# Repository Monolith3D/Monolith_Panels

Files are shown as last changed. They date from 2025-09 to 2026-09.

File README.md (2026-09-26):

# Monolith Panels for Voron 2.4 and Trident

### The 1515 extrusion version by CabbageCorp can be found [here](https://github.com/Monolith3D/Monolith_Panels/tree/main/Usermods/CabbageCorp/Mini_Monolith).

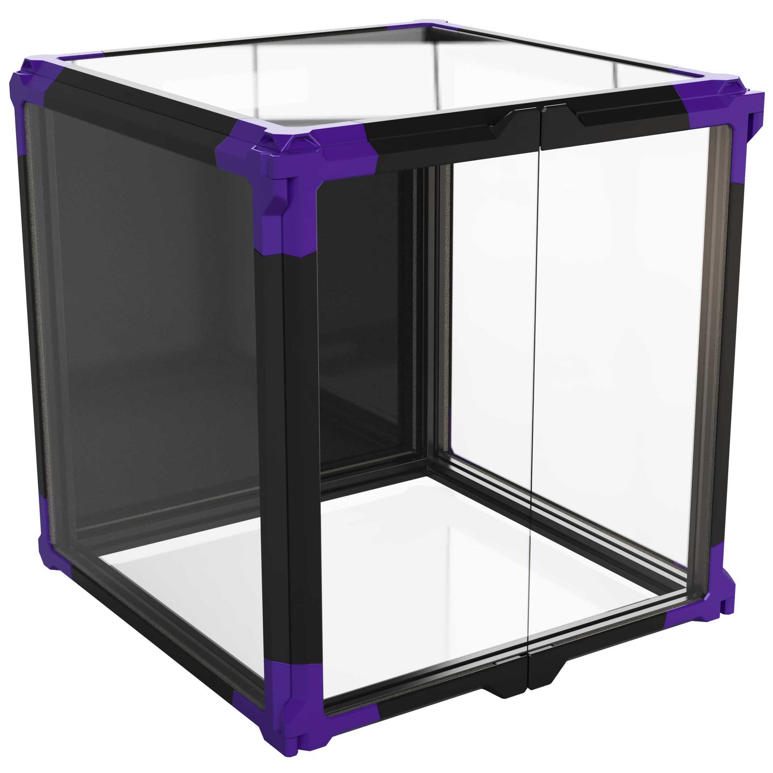
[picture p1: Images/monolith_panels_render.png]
Monolith Panels render


## What's this?

Overcomplicated panels.

## Repository contents

- [CAD](CAD/) - CAD files and assembly reference.
- [STLs](STLs/) - Printable STL files.
- [BOM](BOM/) - Variant BOM CSVs.
- [Images](Images/README.md) - Render gallery.
- [UserMods](Usermods/) - User mods and community additions.

## Use

- The CAD contains everything needed for V2/VT 250/300/350mm with BOM-thickness panels (3mm), and is also a good assembly guide.
- Parts will load in the correct orientation when exported.
- The vertical printed part length is based on theoretical Z travel, not bed size. Pick the vertical part length based on your machine's Z travel. Tridents usually have 250mm Z regardless of bed size, except the cubed kits.
- The panel system is intended to be used with another layer of 3mm foam tape, or with 5mm foam tape paired with 4mm panels. Monolith Gantry stepper protrusion is 4mm.
- The corners can be used without the straights, but your mileage may vary if you do not put VHB on them.
- When used as a panel frame, you can get away with putting VHB only in the middle.
- Clips are fairly sensitive to EM/PA, but can be scaled to fit the other plastic parts. They are not sensitive to aluminum extrusion tolerances.
- Recommended shrinkage compensation for ABS parts is 99.3-99.5%. Test this before committing to large prints, because shrinkage can add up to 3-4mm in total.
- Feel free to remix the parts for different setups.

## Community and support

> [!NOTE]
> **If you have questions or want to stay more up-to-date with Monolith, consider joining the dedicated Discord server.**
>
> Join the Discord (https://discord.gg/monolith3d)
>
> **If you would like to see more of this and other projects in the future, consider supporting Monolith on Patreon.**
>
> Support Monolith on Patreon (https://www.patreon.com/monolith3d)

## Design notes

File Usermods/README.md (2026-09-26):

# User Mods

This folder is for community-made additions, adaptations, and compatibility parts for Monolith Panels.

User mods are not official Monolith Panels files unless stated otherwise. Check the mod author, target printer, panel thickness, door or hinge assumptions, clip style, and clearance assumptions before printing or ordering parts.

Use the folder structure `username/usermod_name` for new user mods.

Good user mod folders should include:

- A short `README.md` explaining what the mod does
- Clear compatibility notes for the target printer, panel dimensions, panel thickness, clip style, and door or hinge setup where relevant
- STL, CAD, image, and BOM files needed to understand the mod
- Assembly notes or warnings if the mod changes panel fit, clips, hinges, handles, door closure, foam stack, or clearance
- Credit and license notes when the mod reuses work from another project

Use user mods at your own risk. They may not receive updates when the main Monolith Panels files change.

## Existing User Mods

| Mod | Author | What it does |
| --- | --- | --- |
| usermod_name | username | Briefly describe what the mod adds, adapts, or changes. |
| [Micronolith Panels](burkfers/Micronolith/) | burkfers | Adapts Mini Monolith panels for a Micron 180, including regular and Formbot vertical variants and Micron R1 handle-compatible horizontals. |
| [Mini Monolith](CabbageCorp/Mini_Monolith/) | CabbageCorp | Adapts Monolith Panels for 1515-extrusion PFA/V0-style printers with ZeroPanels-style clips, panel frames, corners, hinges, and related print files. |
| [Monolith Panels Parametric](mjlo/Monolith%20Panels%20Parametric/) | mjlo | Provides parametric Fusion CAD for Monolith-inspired panels, mainly to support thicker panel material. |
| [Parametric with Annex clips](nvrprfct/parametric_with_annex_clips/) | nvrprfct | Adds Annex-style panel clips and corner/key files to Monolith Panels, with stock-size files and parametric CAD for custom panel stacks. |
| [Middle hinge](SaLei/Middle_hinge/) | SaLei | Provides a middle hinge file and reference image for Monolith Panels. |
| [ClickyClakyMod](TessaKavanagh/ClickyClakyMod/) | TessaKavanagh | Adds spacers and optional replacement ClickyClacky-style parts for adapting the door hinge/latch setup to Monolith Panels. |
|  | your name here :) |  |

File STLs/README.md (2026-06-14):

# STLs

Size-specific horizontal and vertical parts are grouped into subfolders, while shared clips, corners, clamps, and handle parts are kept here at the root.

Use the matching [BOM](../BOM/) to check which files and quantities are needed for a specific panel set.

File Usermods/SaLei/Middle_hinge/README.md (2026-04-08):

# Middle hinges

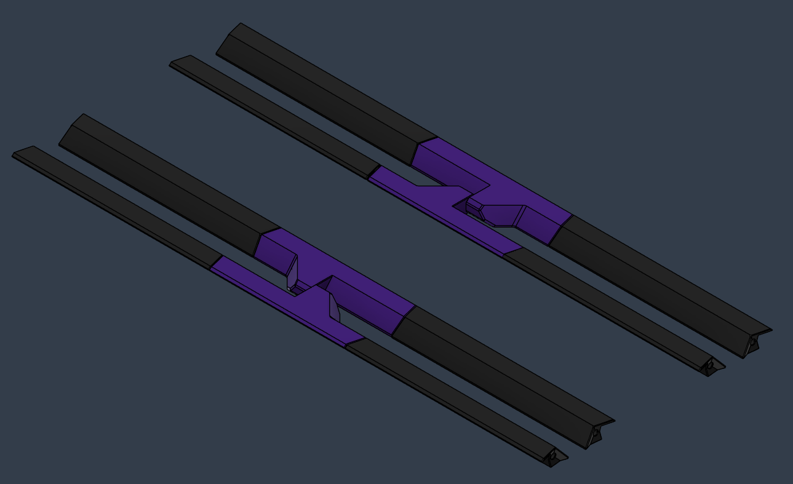
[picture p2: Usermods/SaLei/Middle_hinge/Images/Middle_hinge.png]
Middle_hinge


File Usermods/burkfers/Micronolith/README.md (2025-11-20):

# Micronolith Panels

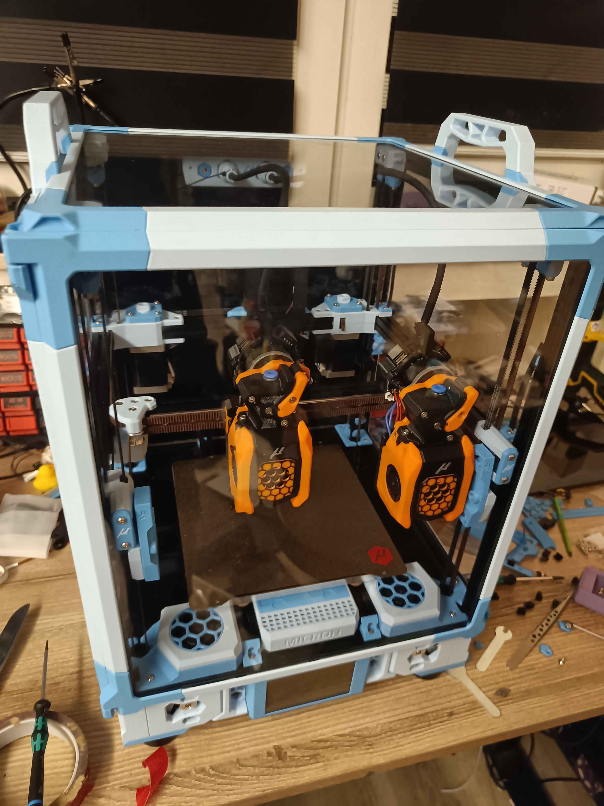
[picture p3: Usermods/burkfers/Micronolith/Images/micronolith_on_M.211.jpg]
Micronolith pannels displayed on M.211


This is an adaptation of CabbageCorp's [Mini Monolith](../../CabbageCorp/Mini_Monolith/) for a Micron 180.

The vertical exists in two variants: Regular, for to-spec panels, and Formbot, whose panels are approximately 2mm taller than the cad vertically.

Side and top horizontals are provided to fit the Micron R1 handles. If you do not wish to use handles, print 4 more horizontals instead.

Please see Mini Monolith for the corner pieces, clips, and more detailed instructions.

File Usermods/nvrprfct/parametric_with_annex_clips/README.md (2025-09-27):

# parametric monolith panels with annex clips
a few files for adding annex clips to the monolith panels. 

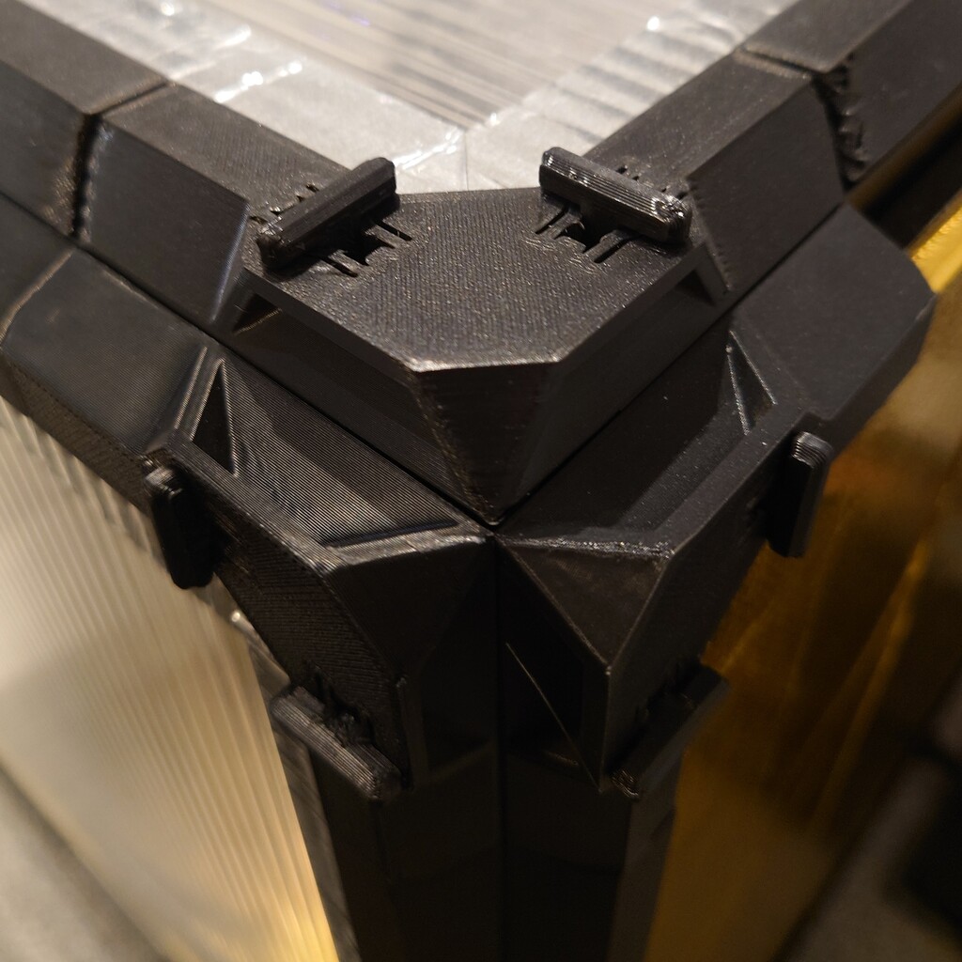
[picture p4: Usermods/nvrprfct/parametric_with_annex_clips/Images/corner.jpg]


## files:
### STLs/monolithStock_annex
- **STLs/monolithStock_annexCorner.step**
- **STLs/monolithStock_annexKey.3mf**

premade files for the stock monolith panel dimensions. you'll still need everything from the original monolith panels, except the corner body. 

print 2x keys for each corner.

### CAD/monolith_annex_mashup_variable_height
- **CAD/monolith_annex_mashup_variable_height.f3d**
- **[key_asymmetric_10.STEP](https://github.com/Annex-Engineering/Annex-Engineering_User_Mods/tree/main/Printers/All_Printers/annex_dev-Panel_2020_Clips_and_Hinges/panel_clips_and_corners/key/CA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)** (or another size)

the full f3d file with parametric history, so that you can custom make your own panel thickness, foam thickness, etc. 
includes corner body, and edge body. does ***not*** include support for hinges, or doors. 
for the key to be the right size, you'll need to download the key from the annex panels repo, split the key in the middle, then lengthen the middle by (panel_height_total - panel_height_outside - key_height - 0.1). where key_height would be 10 for key_asymmetric_10.STEP. 

be warned, I haven't updated the file in a minute, and it might have funny behaviour on large or small heights. I've been meaning to get around to this mod and clean it up, but life happens. 

### credits
[monolith panels by cloakedwayne](https://github.com/Monolith3D/Monolith_Panels)

[annex clips by annex engineering](https://github.com/Annex-Engineering/Annex-Engineering_User_Mods/tree/main/Printers/All_Printers/annex_dev-Panel_2020_Clips_and_Hinges)

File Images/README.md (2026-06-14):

# Preview

| Image | Image |
| --- | --- |
| [<br>Monolith Panels render](monolith_panels_render.png) | [<br>Corner closeup](corner_closeup.png) |
| [<br>Distant view](distant_view.png) | [<br>Inside view](inside.png) |
| [<br>Printed parts spread out](spread_out.png) | [<br>Upside down view](upside_down.png) |

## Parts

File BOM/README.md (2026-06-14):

# Monolith Panels BOM

## V2 250mm

| Amount | Item | Description |
| --- | --- | --- |
| 32 pcs | M3 nut | M3 hex nut. |
| 32 pcs | M3X16 SHCS | Socket head cap screw. |
| 28 pcs | M3X6 BHCS | Button head cap screw. |
| 28 pcs | M3xD5x4 threaded insert | Heat-set threaded insert. |
| 8 m | Foam tape | An additional layer of the same foam 3mm thick tape from the Voron BOM. |
| 1.5 m | VHB tape | VHB tape for adhesive mounting. |
| 0.1 m | 4mm OD PTFE tube | PTFE tube for the hinges. |
| 8 pcs | [`250mm_horizontal_side_x8.stl`](../STLs/Horizontals/250mm_horizontal_side_x8.stl) | Horizontal side piece for the 250mm panel set. |
| 2 pcs | [`250mm_horizontal_door_a_x2.stl`](../STLs/Horizontals/250mm_horizontal_door_a_x2.stl) | Door horizontal printed piece, A. |
| 2 pcs | [`250mm_horizontal_door_b_x2.stl`](../STLs/Horizontals/250mm_horizontal_door_b_x2.stl) | Door horizontal printed piece, B. |
| 6 pcs | [`V2_250mm_vertical_side_x6.stl`](../STLs/Verticals/V2_250mm_vertical_side_x6.stl) | Vertical side piece for the V2 250mm panel set. |
| 12 pcs | [`[a]_corner_x12.stl`](../STLs/%5Ba%5D_corner_x12.stl) | Universal corner printed part. |
| 2 pcs | [`[a]_hinge_a_x2.stl`](../STLs/Hinges/%5Ba%5D_hinge_a_x2.stl) | Universal hinge printed part, A. |
| 2 pcs | [`[a]_hinge_b_x2.stl`](../STLs/Hinges/%5Ba%5D_hinge_b_x2.stl) | Universal hinge printed part, B. |
| 2 pcs | [`[a]_hinge_c_x2.stl`](../STLs/Hinges/%5Ba%5D_hinge_c_x2.stl) | Universal hinge printed part, C. |
| 2 pcs | [`[a]_hinge_d_x2.stl`](../STLs/Hinges/%5Ba%5D_hinge_d_x2.stl) | Universal hinge printed part, D. |
| 60 pcs | [`clip_x60.stl`](../STLs/clip_x60.stl) | Printed panel clip. |
| 20 pcs | [`corner_clamp_BHCS_x20.stl`](../STLs/corner_clamp_BHCS_x20.stl) | Corner clamp for BHCS fastener. |
| 4 pcs | [`door_handle_clamp_x4.stl`](../STLs/door_handle_clamp_x4.stl) | Printed clamp for the door handle. |
| 735.8 cm3 | Total printed part volume | Total printed plastic volume for the printed parts listed above. |
| 650-800 g | Estimated filament use (ABS, Voron settings) | Estimated filament weight for normal unfilled ABS. |
| 700-900 g | Estimated filament use (ABS CF/GF, Voron settings) | Estimated filament weight for filled ABS. |

## V2 300mm

| Amount | Item | Description |
| --- | --- | --- |
| 32 pcs | M3 nut | M3 hex nut. |
| 32 pcs | M3X16 SHCS | Socket head cap screw. |
| 28 pcs | M3X6 BHCS | Button head cap screw. |
| 28 pcs | M3xD5x4 threaded insert | Heat-set threaded insert. |
| 9 m | Foam tape | An additional layer of the same foam 3mm thick tape from the Voron BOM. |
| 1.5 m | VHB tape | VHB tape for adhesive mounting. |
| 0.1 m | 4mm OD PTFE tube | PTFE tube for the hinges. |
| 8 pcs | [`300mm_horizontal_side_x8.stl`](../STLs/Horizontals/300mm_horizontal_side_x8.stl) | Horizontal side piece for the 300mm panel set. |
| 2 pcs | [`300mm_horizontal_door_a_x2.stl`](../STLs/Horizontals/300mm_horizontal_door_a_x2.stl) | Door horizontal printed piece, A. |
| 2 pcs | [`300mm_horizontal_door_b_x2.stl`](../STLs/Horizontals/300mm_horizontal_door_b_x2.stl) | Door horizontal printed piece, B. |
| 6 pcs | [`V2_300mm_vertical_side_x6.stl`](../STLs/Verticals/V2_300mm_vertical_side_x6.stl) | Vertical side piece for the V2 300mm panel set. |
| 12 pcs | [`[a]_corner_x12.stl`](../STLs/%5Ba%5D_corner_x12.stl) | Universal corner printed part. |
| 2 pcs | [`[a]_hinge_a_x2.stl`](../STLs/Hinges/%5Ba%5D_hinge_a_x2.stl) | Universal hinge printed part, A. |
| 2 pcs | [`[a]_hinge_b_x2.stl`](../STLs/Hinges/%5Ba%5D_hinge_b_x2.stl) | Universal hinge printed part, B. |
| 2 pcs | [`[a]_hinge_c_x2.stl`](../STLs/Hinges/%5Ba%5D_hinge_c_x2.stl) | Universal hinge printed part, C. |
| 2 pcs | [`[a]_hinge_d_x2.stl`](../STLs/Hinges/%5Ba%5D_hinge_d_x2.stl) | Universal hinge printed part, D. |
| 60 pcs | [`clip_x60.stl`](../STLs/clip_x60.stl) | Printed panel clip. |
| 20 pcs | [`corner_clamp_BHCS_x20.stl`](../STLs/corner_clamp_BHCS_x20.stl) | Corner clamp for BHCS fastener. |
| 4 pcs | [`door_handle_clamp_x4.stl`](../STLs/door_handle_clamp_x4.stl) | Printed clamp for the door handle. |
| 824.9 cm3 | Total printed part volume | Total printed plastic volume for the printed parts listed above. |
| 700-900 g | Estimated filament use (ABS, Voron settings) | Estimated filament weight for normal unfilled ABS. |
| 750-1000 g | Estimated filament use (ABS CF/GF, Voron settings) | Estimated filament weight for filled ABS. |

## V2 350mm

| Amount | Item | Description |
| --- | --- | --- |
| 32 pcs | M3 nut | M3 hex nut. |
| 32 pcs | M3X16 SHCS | Socket head cap screw. |
| 28 pcs | M3X6 BHCS | Button head cap screw. |
| 28 pcs | M3xD5x4 threaded insert | Heat-set threaded insert. |
| 9 m | Foam tape | An additional layer of the same foam 3mm thick tape from the Voron BOM. |
| 1.5 m | VHB tape | VHB tape for adhesive mounting. |
| 0.1 m | 4mm OD PTFE tube | PTFE tube for the hinges. |
| 8 pcs | [`350mm_horizontal_side_x8.stl`](../STLs/Horizontals/350mm_horizontal_side_x8.stl) | Horizontal side piece for the 350mm panel set. |
| 2 pcs | [`350mm_horizontal_door_a_x2.stl`](../STLs/Horizontals/350mm_horizontal_door_a_x2.stl) | Door horizontal printed piece, A. |
| 2 pcs | [`350mm_horizontal_door_b_x2.stl`](../STLs/Horizontals/350mm_horizontal_door_b_x2.stl) | Door horizontal printed piece, B. |
| 6 pcs | [`V2_350mm_vertical_side_x6.stl`](../STLs/Verticals/V2_350mm_vertical_side_x6.stl) | Vertical side piece for the V2 350mm panel set. |
| 12 pcs | [`[a]_corner_x12.stl`](../STLs/%5Ba%5D_corner_x12.stl) | Universal corner printed part. |
| 2 pcs | [`[a]_hinge_a_x2.stl`](../STLs/Hinges/%5Ba%5D_hinge_a_x2.stl) | Universal hinge printed part, A. |
| 2 pcs | [`[a]_hinge_b_x2.stl`](../STLs/Hinges/%5Ba%5D_hinge_b_x2.stl) | Universal hinge printed part, B. |
| 2 pcs | [`[a]_hinge_c_x2.stl`](../STLs/Hinges/%5Ba%5D_hinge_c_x2.stl) | Universal hinge printed part, C. |
| 2 pcs | [`[a]_hinge_d_x2.stl`](../STLs/Hinges/%5Ba%5D_hinge_d_x2.stl) | Universal hinge printed part, D. |
| 60 pcs | [`clip_x60.stl`](../STLs/clip_x60.stl) | Printed panel clip. |
| 20 pcs | [`corner_clamp_BHCS_x20.stl`](../STLs/corner_clamp_BHCS_x20.stl) | Corner clamp for BHCS fastener. |
| 4 pcs | [`door_handle_clamp_x4.stl`](../STLs/door_handle_clamp_x4.stl) | Printed clamp for the door handle. |
| 914.0 cm3 | Total printed part volume | Total printed plastic volume for the printed parts listed above. |
| 800-950 g | Estimated filament use (ABS, Voron settings) | Estimated filament weight for normal unfilled ABS. |
| 850-1100 g | Estimated filament use (ABS CF/GF, Voron settings) | Estimated filament weight for filled ABS. |

## VT 250mm

| Amount | Item | Description |
| --- | --- | --- |
| 38 pcs | M3 nut | M3 hex nut. |
| 38 pcs | M3X16 SHCS | Socket head cap screw. |
| 28 pcs | M3X6 BHCS | Button head cap screw. |
| 28 pcs | M3xD5x4 threaded insert | Heat-set threaded insert. |
| - | Split vertical joints | Includes +6 M3X16 SHCS and +6 M3 nut for the 6 vertical segment joints. |
| 8 m | Foam tape | An additional layer of the same foam 3mm thick tape from the Voron BOM. |
| 1.5 m | VHB tape | VHB tape for adhesive mounting. |
| 0.1 m | 4mm OD PTFE tube | PTFE tube for the hinges. |
| 8 pcs | [`250mm_horizontal_side_x8.stl`](../STLs/Horizontals/250mm_horizontal_side_x8.stl) | Horizontal side piece for the 250mm panel set. |
| 2 pcs | [`250mm_horizontal_door_a_x2.stl`](../STLs/Horizontals/250mm_horizontal_door_a_x2.stl) | Door horizontal printed piece, A. |
| 2 pcs | [`250mm_horizontal_door_b_x2.stl`](../STLs/Horizontals/250mm_horizontal_door_b_x2.stl) | Door horizontal printed piece, B. |
| 6 pcs | [`VT_250mm_vertical_side_a_x6.stl`](../STLs/Verticals/VT_250mm_vertical_side_a_x6.stl) | Vertical side piece for the VT 250mm panel set, A. |
| 6 pcs | [`VT_250mm_vertical_side_b_x6.stl`](../STLs/Verticals/VT_250mm_vertical_side_b_x6.stl) | Vertical side piece for the VT 250mm panel set, B. |
| 12 pcs | [`[a]_corner_x12.stl`](../STLs/%5Ba%5D_corner_x12.stl) | Universal corner printed part. |
| 2 pcs | [`[a]_hinge_a_x2.stl`](../STLs/Hinges/%5Ba%5D_hinge_a_x2.stl) | Universal hinge printed part, A. |
| 2 pcs | [`[a]_hinge_b_x2.stl`](../STLs/Hinges/%5Ba%5D_hinge_b_x2.stl) | Universal hinge printed part, B. |
| 2 pcs | [`[a]_hinge_c_x2.stl`](../STLs/Hinges/%5Ba%5D_hinge_c_x2.stl) | Universal hinge printed part, C. |
| 2 pcs | [`[a]_hinge_d_x2.stl`](../STLs/Hinges/%5Ba%5D_hinge_d_x2.stl) | Universal hinge printed part, D. |
| 60 pcs | [`clip_x60.stl`](../STLs/clip_x60.stl) | Printed panel clip. |
| 20 pcs | [`corner_clamp_BHCS_x20.stl`](../STLs/corner_clamp_BHCS_x20.stl) | Corner clamp for BHCS fastener. |
| 4 pcs | [`door_handle_clamp_x4.stl`](../STLs/door_handle_clamp_x4.stl) | Printed clamp for the door handle. |
| 772.1 cm3 | Total printed part volume | Total printed plastic volume for the printed parts listed above. |
| 700-850 g | Estimated filament use (ABS, Voron settings) | Estimated filament weight for normal unfilled ABS. |
| 700-950 g | Estimated filament use (ABS CF/GF, Voron settings) | Estimated filament weight for filled ABS. |

## VT 300mm

| Amount | Item | Description |
| --- | --- | --- |
| 38 pcs | M3 nut | M3 hex nut. |
| 38 pcs | M3X16 SHCS | Socket head cap screw. |
| 28 pcs | M3X6 BHCS | Button head cap screw. |
| 28 pcs | M3xD5x4 threaded insert | Heat-set threaded insert. |
| - | Split vertical joints | Includes +6 M3X16 SHCS and +6 M3 nut for the 6 vertical segment joints. |
| 9 m | Foam tape | An additional layer of the same foam 3mm thick tape from the Voron BOM. |
| 1.5 m | VHB tape | VHB tape for adhesive mounting. |
| 0.1 m | 4mm OD PTFE tube | PTFE tube for the hinges. |
| 8 pcs | [`300mm_horizontal_side_x8.stl`](../STLs/Horizontals/300mm_horizontal_side_x8.stl) | Horizontal side piece for the 300mm panel set. |
| 2 pcs | [`300mm_horizontal_door_a_x2.stl`](../STLs/Horizontals/300mm_horizontal_door_a_x2.stl) | Door horizontal printed piece, A. |
| 2 pcs | [`300mm_horizontal_door_b_x2.stl`](../STLs/Horizontals/300mm_horizontal_door_b_x2.stl) | Door horizontal printed piece, B. |
| 6 pcs | [`VT_250mm_vertical_side_a_x6.stl`](../STLs/Verticals/VT_250mm_vertical_side_a_x6.stl) | Vertical side piece for VT 250mm Z, A. |
| 6 pcs | [`VT_250mm_vertical_side_b_x6.stl`](../STLs/Verticals/VT_250mm_vertical_side_b_x6.stl) | Vertical side piece for VT 250mm Z, B. |
| 12 pcs | [`[a]_corner_x12.stl`](../STLs/%5Ba%5D_corner_x12.stl) | Universal corner printed part. |
| 2 pcs | [`[a]_hinge_a_x2.stl`](../STLs/Hinges/%5Ba%5D_hinge_a_x2.stl) | Universal hinge printed part, A. |
| 2 pcs | [`[a]_hinge_b_x2.stl`](../STLs/Hinges/%5Ba%5D_hinge_b_x2.stl) | Universal hinge printed part, B. |
| 2 pcs | [`[a]_hinge_c_x2.stl`](../STLs/Hinges/%5Ba%5D_hinge_c_x2.stl) | Universal hinge printed part, C. |
| 2 pcs | [`[a]_hinge_d_x2.stl`](../STLs/Hinges/%5Ba%5D_hinge_d_x2.stl) | Universal hinge printed part, D. |
| 60 pcs | [`clip_x60.stl`](../STLs/clip_x60.stl) | Printed panel clip. |
| 20 pcs | [`corner_clamp_BHCS_x20.stl`](../STLs/corner_clamp_BHCS_x20.stl) | Corner clamp for BHCS fastener. |
| 4 pcs | [`door_handle_clamp_x4.stl`](../STLs/door_handle_clamp_x4.stl) | Printed clamp for the door handle. |
| 827.8 cm3 | Total printed part volume | Total printed plastic volume for the printed parts listed above. |
| 750-900 g | Estimated filament use (ABS, Voron settings) | Estimated filament weight for normal unfilled ABS. |
| 800-1000 g | Estimated filament use (ABS CF/GF, Voron settings) | Estimated filament weight for filled ABS. |

## VT 300mm Cube

| Amount | Item | Description |
| --- | --- | --- |
| 38 pcs | M3 nut | M3 hex nut. |
| 38 pcs | M3X16 SHCS | Socket head cap screw. |
| 28 pcs | M3X6 BHCS | Button head cap screw. |
| 28 pcs | M3xD5x4 threaded insert | Heat-set threaded insert. |
| - | Split vertical joints | Includes +6 M3X16 SHCS and +6 M3 nut for the 6 vertical segment joints. |
| 9 m | Foam tape | An additional layer of the same foam 3mm thick tape from the Voron BOM. |
| 1.5 m | VHB tape | VHB tape for adhesive mounting. |
| 0.1 m | 4mm OD PTFE tube | PTFE tube for the hinges. |
| 8 pcs | [`300mm_horizontal_side_x8.stl`](../STLs/Horizontals/300mm_horizontal_side_x8.stl) | Horizontal side piece for the 300mm panel set. |
| 2 pcs | [`300mm_horizontal_door_a_x2.stl`](../STLs/Horizontals/300mm_horizontal_door_a_x2.stl) | Door horizontal printed piece, A. |
| 2 pcs | [`300mm_horizontal_door_b_x2.stl`](../STLs/Horizontals/300mm_horizontal_door_b_x2.stl) | Door horizontal printed piece, B. |
| 6 pcs | [`VT_300mm_vertical_side_a_x6.stl`](../STLs/Verticals/VT_300mm_vertical_side_a_x6.stl) | Vertical side piece for the VT 300mm panel set, A. |
| 6 pcs | [`VT_300mm_vertical_side_b_x6.stl`](../STLs/Verticals/VT_300mm_vertical_side_b_x6.stl) | Vertical side piece for the VT 300mm panel set, B. |
| 12 pcs | [`[a]_corner_x12.stl`](../STLs/%5Ba%5D_corner_x12.stl) | Universal corner printed part. |
| 2 pcs | [`[a]_hinge_a_x2.stl`](../STLs/Hinges/%5Ba%5D_hinge_a_x2.stl) | Universal hinge printed part, A. |
| 2 pcs | [`[a]_hinge_b_x2.stl`](../STLs/Hinges/%5Ba%5D_hinge_b_x2.stl) | Universal hinge printed part, B. |
| 2 pcs | [`[a]_hinge_c_x2.stl`](../STLs/Hinges/%5Ba%5D_hinge_c_x2.stl) | Universal hinge printed part, C. |
| 2 pcs | [`[a]_hinge_d_x2.stl`](../STLs/Hinges/%5Ba%5D_hinge_d_x2.stl) | Universal hinge printed part, D. |
| 60 pcs | [`clip_x60.stl`](../STLs/clip_x60.stl) | Printed panel clip. |
| 20 pcs | [`corner_clamp_BHCS_x20.stl`](../STLs/corner_clamp_BHCS_x20.stl) | Corner clamp for BHCS fastener. |
| 4 pcs | [`door_handle_clamp_x4.stl`](../STLs/door_handle_clamp_x4.stl) | Printed clamp for the door handle. |
| 861.3 cm3 | Total printed part volume | Total printed plastic volume for the printed parts listed above. |
| 750-900 g | Estimated filament use (ABS, Voron settings) | Estimated filament weight for normal unfilled ABS. |
| 800-1050 g | Estimated filament use (ABS CF/GF, Voron settings) | Estimated filament weight for filled ABS. |

## VT 350mm

| Amount | Item | Description |
| --- | --- | --- |
| 38 pcs | M3 nut | M3 hex nut. |
| 38 pcs | M3X16 SHCS | Socket head cap screw. |
| 28 pcs | M3X6 BHCS | Button head cap screw. |
| 28 pcs | M3xD5x4 threaded insert | Heat-set threaded insert. |
| - | Split vertical joints | Includes +6 M3X16 SHCS and +6 M3 nut for the 6 vertical segment joints. |
| 9 m | Foam tape | An additional layer of the same foam 3mm thick tape from the Voron BOM. |
| 1.5 m | VHB tape | VHB tape for adhesive mounting. |
| 0.1 m | 4mm OD PTFE tube | PTFE tube for the hinges. |
| 8 pcs | [`350mm_horizontal_side_x8.stl`](../STLs/Horizontals/350mm_horizontal_side_x8.stl) | Horizontal side piece for the 350mm panel set. |
| 2 pcs | [`350mm_horizontal_door_a_x2.stl`](../STLs/Horizontals/350mm_horizontal_door_a_x2.stl) | Door horizontal printed piece, A. |
| 2 pcs | [`350mm_horizontal_door_b_x2.stl`](../STLs/Horizontals/350mm_horizontal_door_b_x2.stl) | Door horizontal printed piece, B. |
| 6 pcs | [`VT_250mm_vertical_side_a_x6.stl`](../STLs/Verticals/VT_250mm_vertical_side_a_x6.stl) | Vertical side piece for VT 250mm Z, A. |
| 6 pcs | [`VT_250mm_vertical_side_b_x6.stl`](../STLs/Verticals/VT_250mm_vertical_side_b_x6.stl) | Vertical side piece for VT 250mm Z, B. |
| 12 pcs | [`[a]_corner_x12.stl`](../STLs/%5Ba%5D_corner_x12.stl) | Universal corner printed part. |
| 2 pcs | [`[a]_hinge_a_x2.stl`](../STLs/Hinges/%5Ba%5D_hinge_a_x2.stl) | Universal hinge printed part, A. |
| 2 pcs | [`[a]_hinge_b_x2.stl`](../STLs/Hinges/%5Ba%5D_hinge_b_x2.stl) | Universal hinge printed part, B. |
| 2 pcs | [`[a]_hinge_c_x2.stl`](../STLs/Hinges/%5Ba%5D_hinge_c_x2.stl) | Universal hinge printed part, C. |
| 2 pcs | [`[a]_hinge_d_x2.stl`](../STLs/Hinges/%5Ba%5D_hinge_d_x2.stl) | Universal hinge printed part, D. |
| 60 pcs | [`clip_x60.stl`](../STLs/clip_x60.stl) | Printed panel clip. |
| 20 pcs | [`corner_clamp_BHCS_x20.stl`](../STLs/corner_clamp_BHCS_x20.stl) | Corner clamp for BHCS fastener. |
| 4 pcs | [`door_handle_clamp_x4.stl`](../STLs/door_handle_clamp_x4.stl) | Printed clamp for the door handle. |
| 883.5 cm3 | Total printed part volume | Total printed plastic volume for the printed parts listed above. |
| 800-950 g | Estimated filament use (ABS, Voron settings) | Estimated filament weight for normal unfilled ABS. |
| 850-1100 g | Estimated filament use (ABS CF/GF, Voron settings) | Estimated filament weight for filled ABS. |

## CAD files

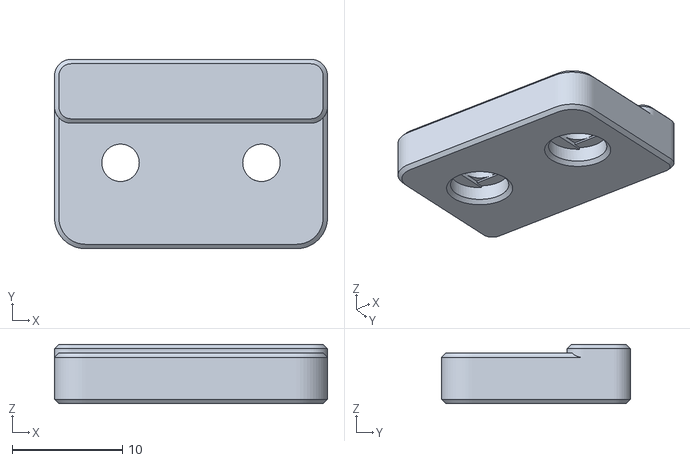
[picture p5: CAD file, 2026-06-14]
STLs/door_handle_clamp_x4.stl
24.8 x 17.2 x 5.40

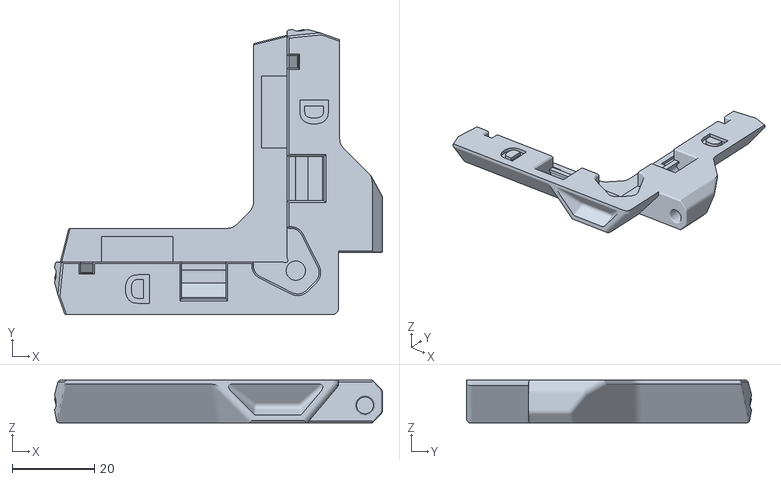
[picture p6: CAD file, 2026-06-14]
STLs/Hinges/[a]_hinge_d_x2.stl
79.8 x 69.4 x 10.4

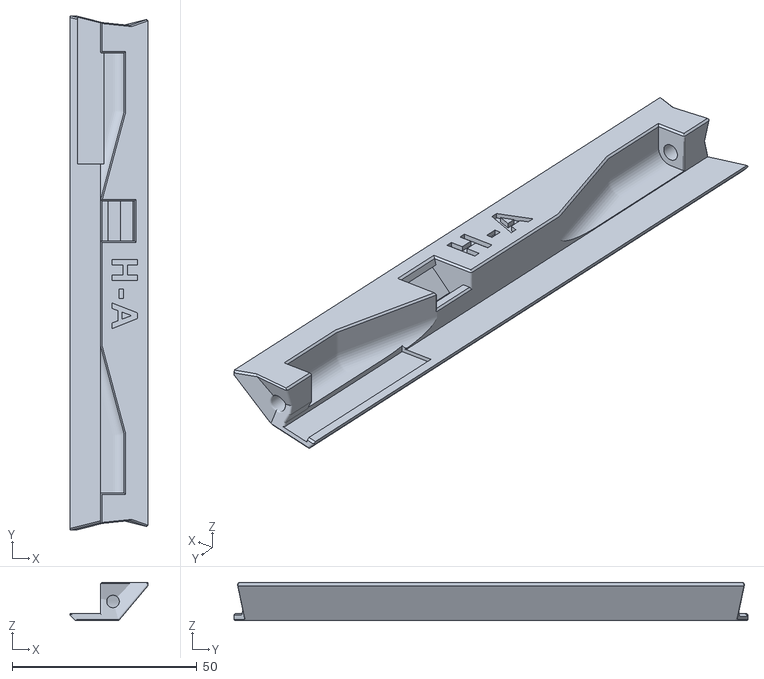
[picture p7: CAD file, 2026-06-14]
STLs/Horizontals/250mm_horizontal_side_a_x8.stl
21.0 x 139.0 x 10.4

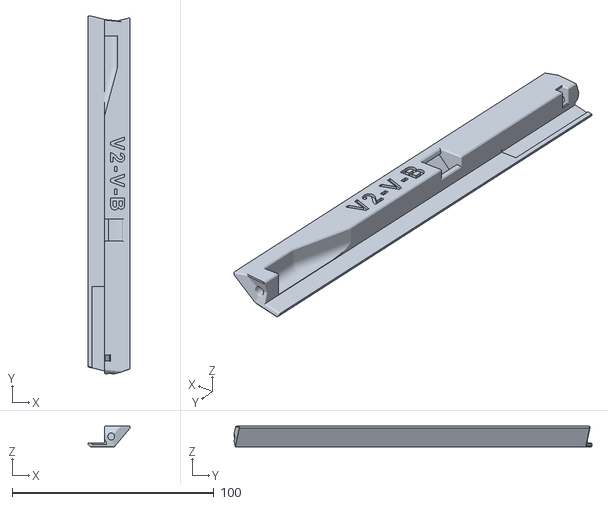
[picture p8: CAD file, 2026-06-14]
STLs/Verticals/V2_300mm_vertical_side_b_x6.stl
21.0 x 177.4 x 10.4

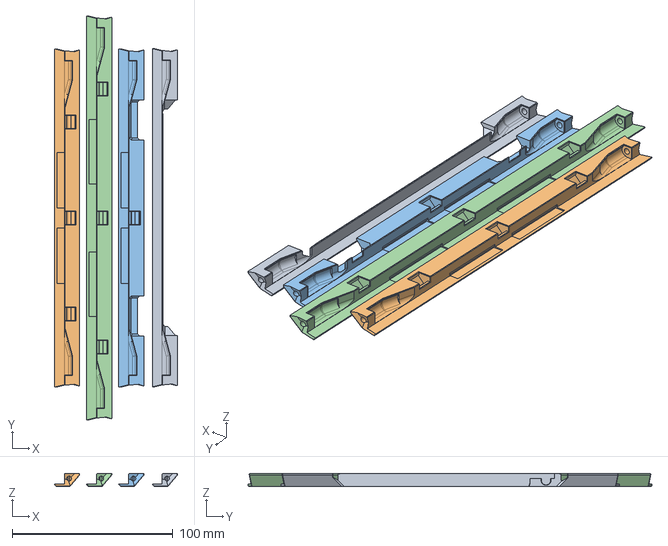
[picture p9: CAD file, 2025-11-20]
Usermods/burkfers/Micronolith/CAD/Micronolith_straights.step
76.6 x 251.2 x 7.80 mm

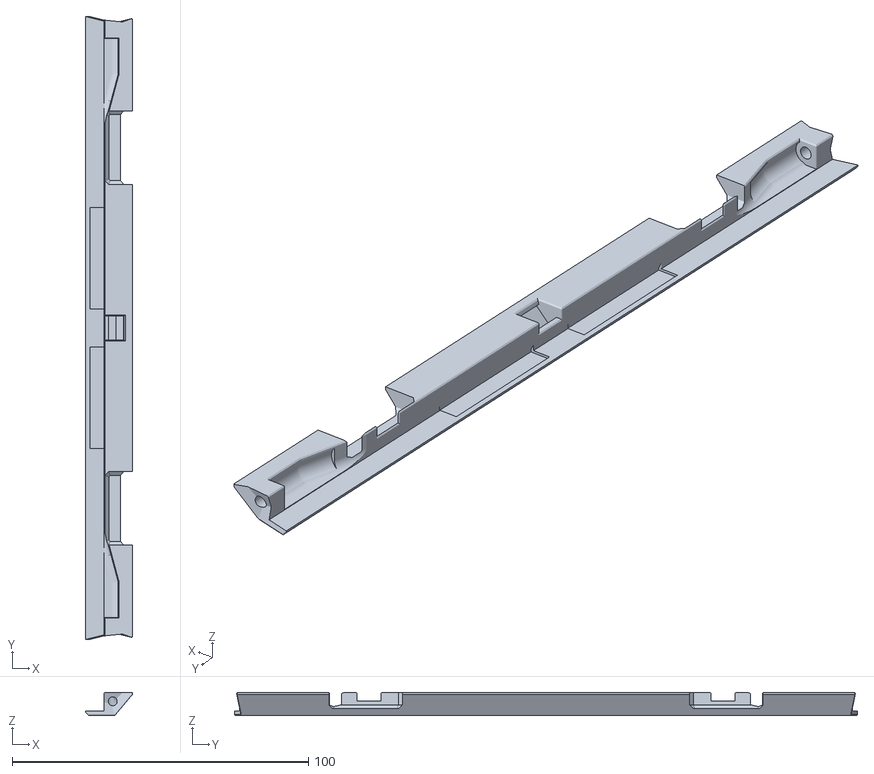
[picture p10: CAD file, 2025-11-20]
Usermods/burkfers/Micronolith/STLs/Micronolith_Horizontal_HandleSide_x2.stl
15.8 x 210.4 x 7.80

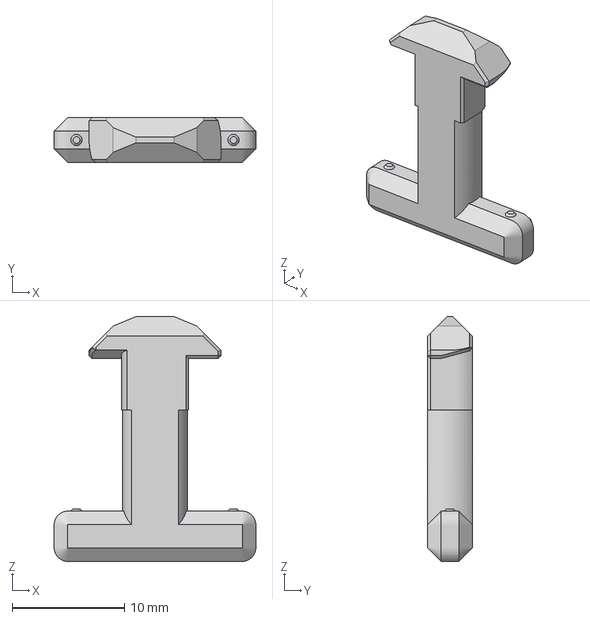
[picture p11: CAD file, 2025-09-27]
Usermods/nvrprfct/parametric_with_annex_clips/STLs/monolithStock_annexKey.3mf
18.0 x 4.00 x 21.9 mm

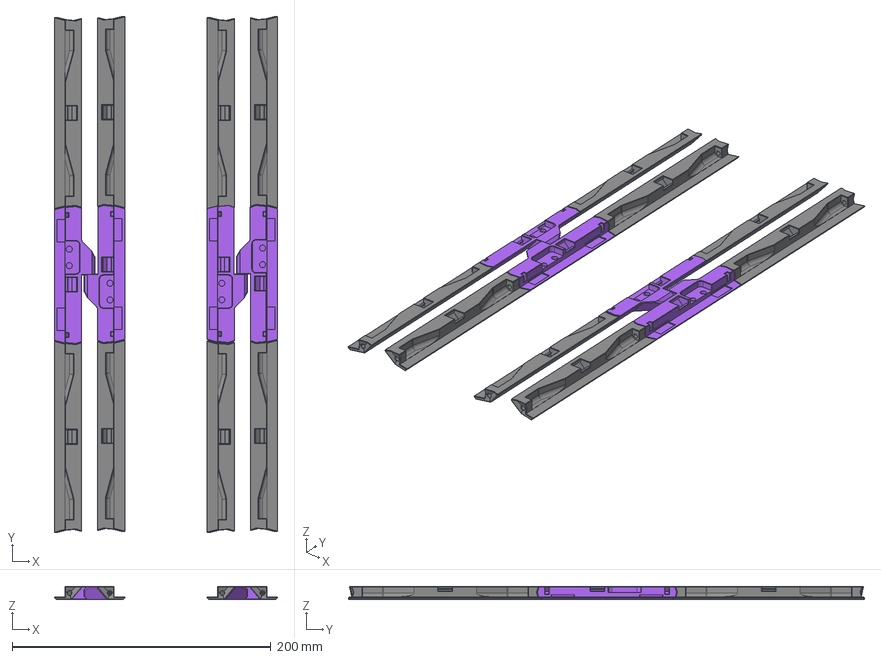
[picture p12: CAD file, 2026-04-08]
Usermods/SaLei/Middle_hinge/CAD/Monolith_Panels_middle_hinge_by_SaLei.step
172.3 x 398.8 x 10.4 mm
Mid hinge B1
Vertical side split for mid hinge x 8

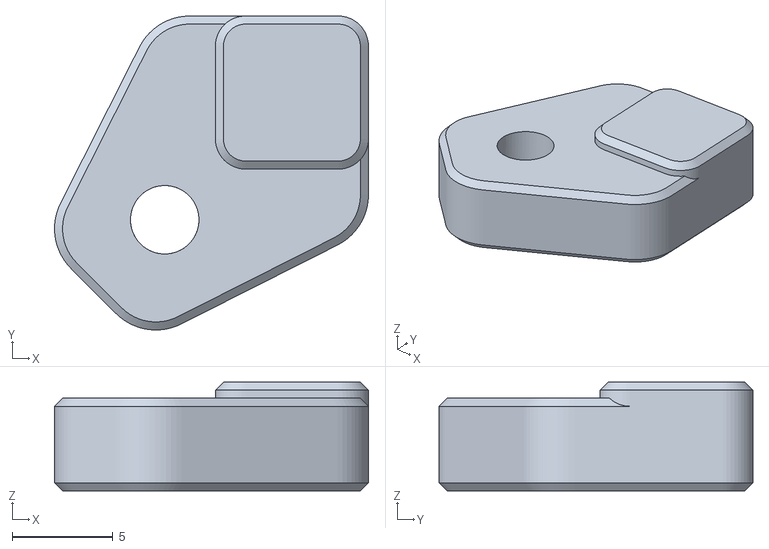
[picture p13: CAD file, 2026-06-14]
STLs/corner_clamp_FHCS_x20.stl
15.6 x 15.6 x 5.40

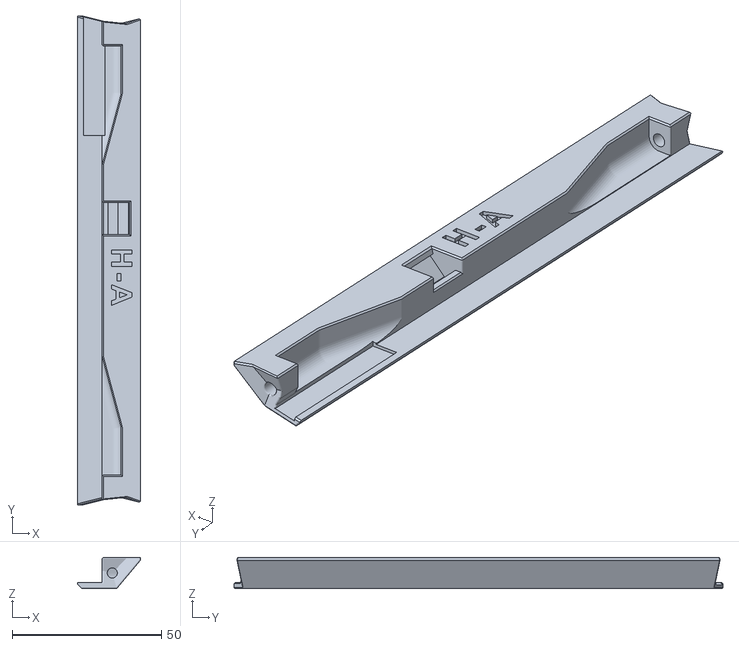
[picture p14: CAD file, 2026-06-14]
STLs/Horizontals/300mm_horizontal_side_a_x8.stl
21.0 x 164.0 x 10.4

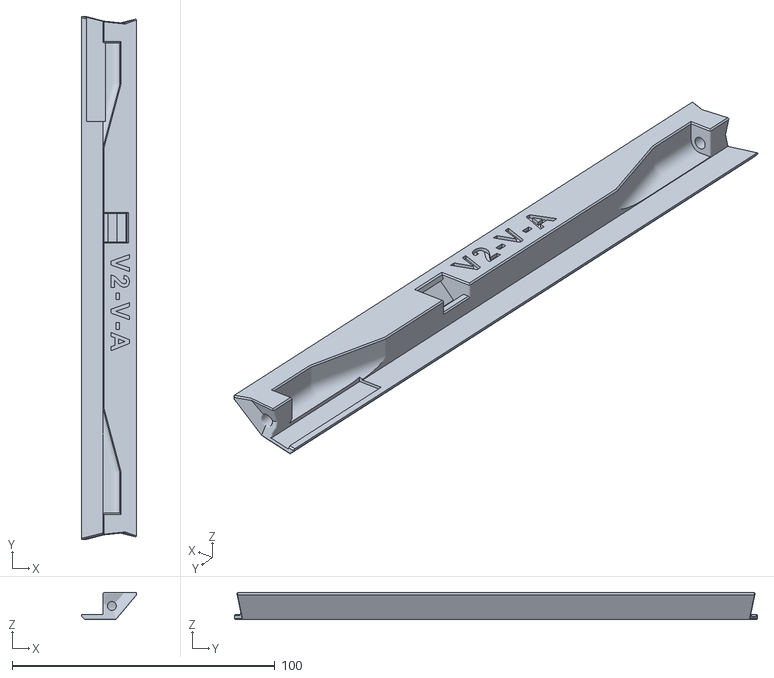
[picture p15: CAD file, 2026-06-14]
STLs/Verticals/V2_350mm_vertical_side_a_x6.stl
21.0 x 199.0 x 10.4

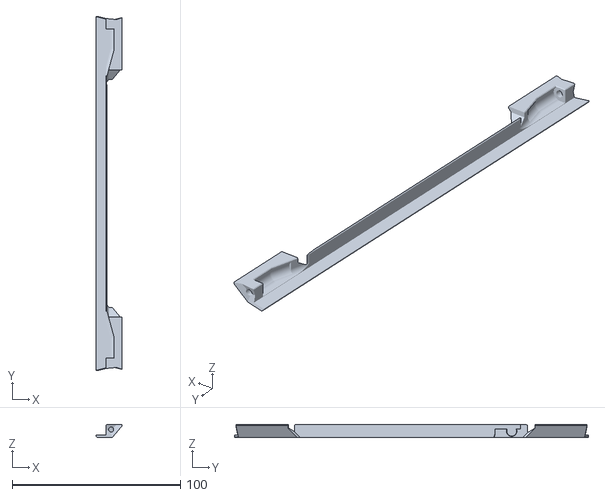
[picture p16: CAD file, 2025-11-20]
Usermods/burkfers/Micronolith/STLs/Micronolith_Horizontal_HandleTop_x2.stl
15.8 x 210.4 x 7.80

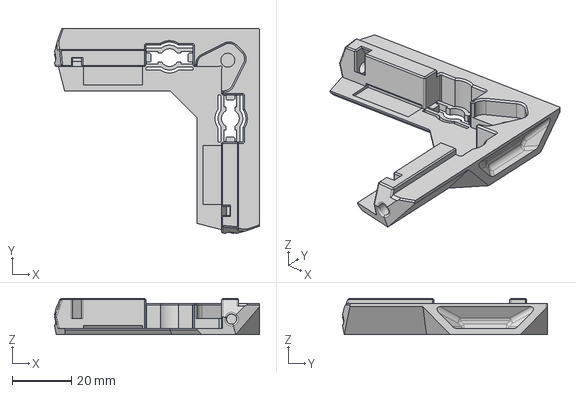
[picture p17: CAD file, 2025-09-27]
Usermods/nvrprfct/parametric_with_annex_clips/STLs/monolithStock_annexCorner.step
69.1 x 69.1 x 12.2 mm

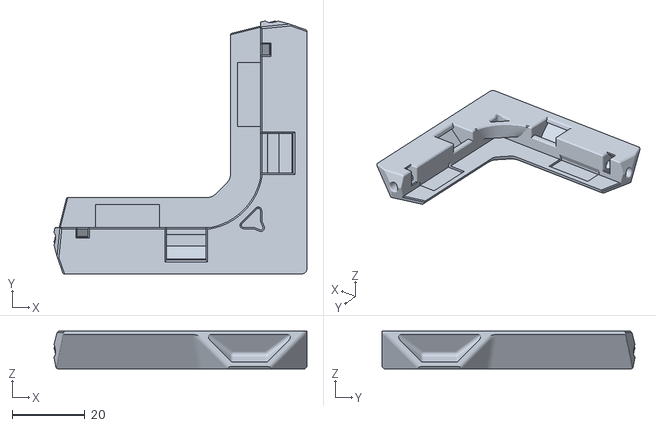
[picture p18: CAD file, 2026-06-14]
STLs/[a]_experimental_clampless_corner.stl
69.4 x 69.4 x 10.4

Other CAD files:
STLs/Hinges/[a]_hinge_b_x2.stl
Usermods/burkfers/Micronolith/CAD/Micronolith_straights_Formbot.step
STLs/Hinges/[a]_hinge_a_x2.stl
STLs/Horizontals/350mm_horizontal_side_x8.stl
STLs/Hinges/[a]_hinge_c_x2.stl
STLs/Horizontals/250mm_horizontal_door_a_x2.stl
STLs/Horizontals/250mm_horizontal_door_b_x2.stl
STLs/Horizontals/250mm_horizontal_side_b_x8.stl
STLs/Horizontals/250mm_horizontal_side_x8.stl
STLs/Horizontals/300mm_horizontal_door_a_x2.stl
STLs/Horizontals/300mm_horizontal_door_b_x2.stl
STLs/Horizontals/300mm_horizontal_side_b_x8.stl
STLs/Horizontals/300mm_horizontal_side_x8.stl
STLs/Horizontals/350mm_horizontal_door_a_x2.stl
STLs/Horizontals/350mm_horizontal_door_b_x2.stl
STLs/Horizontals/350mm_horizontal_side_a_x8.stl
STLs/Horizontals/350mm_horizontal_side_b_x8.stl
STLs/Verticals/V2_250mm_vertical_side_a_x6.stl
STLs/Verticals/V2_250mm_vertical_side_b_x6.stl
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

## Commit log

2025-11-20 Add Micronolith Panels
    [Micronolith_Formbot_Vertical_x6.stl, Micronolith_Horizontal_HandleSide_x2.stl, Micronolith_Horizontal_HandleTop_x2.stl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]
2026-04-08 middle hinge mod
    [Monolith_Panels_middle_hinge_by_SaLei.step]
2026-06-14 BOM and STLs added
    [250mm_horizontal_door_a_x2.stl, 250mm_horizontal_door_b_x2.stl, 250mm_horizontal_side_a_x8.stl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]
